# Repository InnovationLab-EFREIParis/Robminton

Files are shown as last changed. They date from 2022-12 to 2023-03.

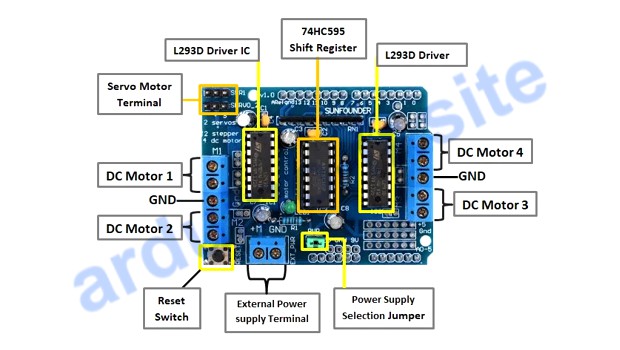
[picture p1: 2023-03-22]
03_ElecCode/1. Ramasseur/1. L293D Motor Drive Arduino Shield/1. Schematic/Components Schematic.jpg

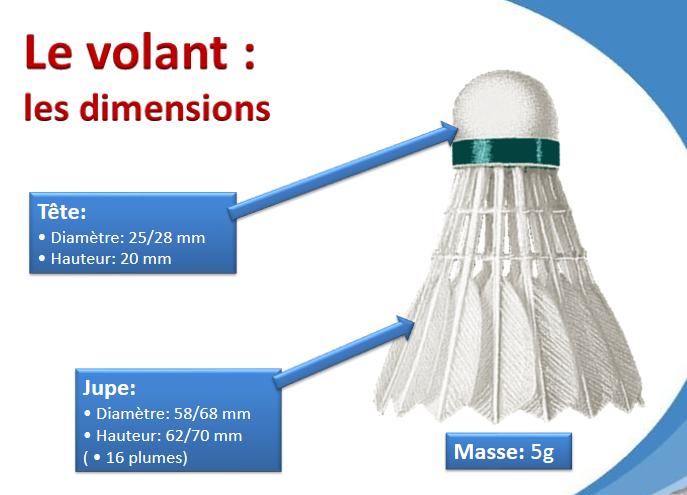
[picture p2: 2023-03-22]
03_ElecCode/0. Cave/dimension de volant.PNG

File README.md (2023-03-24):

# Robminton

Le projet a pour but de répondre à l'appel d'offre fait par la FFB (Fédération Française de Badminton). Il est composé de 2 parties, un robot ramasseur de volants ainsi qu'un robot lanceur de volants. Même si ce genre de produits existe déjà sur le marché (surtout côté lanceur) le but est quand même de produire un robot plus performant, open source et à moindre coût. 

Concernant les logiciels à avoir, il est nécessaire d'avoir SolidWorks afin d'utiliser au mieux les fichiers SW des pièces que nous avons modélisés. Il est aussi recommandé d'avoir un IDE (type CodeBlocks) pour tout ce qui est programme en C (calculatrice de paramètres du lanceur). Posséder une machine virtuel avec ROS et un IDE pour la programmation sur ST32 (type CubeIDE). 

Toutes les ressources que nous avons utilisées/produites sont présentes dans le git :

00_doc : contient toute la documentation que nous avons utilisé ou produit pendant le projet

01_mdl : contient les modélisation 3D que nous avons faites au cours du projet. Dedans ce sera le dossier SW qui sera le plus utile. Toutes les pièces/assemblages y sont. 

02_src : contient tout les codes sources utilisés pour faire fonctionner les moteurs présents dans nos robots. 

03_elec : contient de la documentation détaillée de toute l'électronique que nous utilisons que ce soit les cartes embarquées ou bien les moteurs. 

Nous avons fait en sorte que le projet parte sur de bonnes bases afin que les prochains groupes puissent travailler sur la partie plus intéressante du projet c'est à dire faire des tests. La modélisation du châssis du robot ramasseur est faite, il ne manque que quelques découpes à faire et des équerres à commander. Les moteurs fonctionnent avec le code que nous avons mis sur le Git il suffira de gérer les 4 moteurs en même temps. Le chemin pour y arriver est le suivant : Robminton/03_elec/1. Ramasseur/3. STM32 Nucleo-64/0. Code/1. L293D Motor1 Drive Arduino Shield/L293_Shield/

Il faudra cependant trouver une solution pour que le robot puisse ramasser tout les volants (plusieurs centaines de volants) rapidment donc sûrement revoir le système de stockage. Niveau lanceur toute la partie théorique à été faite et donc ne sera plus à refaire. Un dispositif pour le lanceur a été mis en place il ne reste qu'à l'implémenter sur une structure (en profilé), un croquis est disponible dans 00_src pour mieux comprendre. 

Le matériel que nous avons utilisé sera présent dans le casier Robminton à l'I-lab, ou bien sera à récupérer auprès des encadrants du projet (Rémi GRIOT/Elizabeth Colin). Un inventaire sera aussi disponible dans le dossier 00_doc afin que les prochains groupes puissent savoir ce qu'il manque, ce qu'il commander ...

Equipe : AMADO Daniel, BERBEROVIC Amon, LIENG Antoine, PUSZYNSKI Hugo, VACHEROT Tristan

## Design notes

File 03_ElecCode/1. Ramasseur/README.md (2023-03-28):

# Ramasseur Folder
Ce dossier contient tous les codes et documentations du ramasseur.

## Contenu des fichiers
* `1. L293D Motor Drive Arduino Shield`: ce dossier est consacré à la carte conçu pour être utilisée avec la carte STM32 pour contrôler les moteurs du robot.
* `2. CQRobot DC Geared Motor with Encoder`: ce dossier est consacré aux moteurs électriques à courant continu à engrenages avec un encodeur intégré.
* `3. STM32 Nucleo-64`: ce dossier est consacré aux codes et aux schémas électroniques entre la carte STM32 et les autres composants du robot.
* `4. Raspberry Pi3`: ce dossier est consacré aux programmes et aux librairies utilisés pour manipuler la carte STM32 avec une Raspberry.

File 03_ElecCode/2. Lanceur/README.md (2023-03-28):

# Lanceur Folder
Ce dossier contient tous les codes et documentations du lanceur.

## Contenu des fichiers
* `1. Racerstar BR2306S 2400KV`: ce dossier est consacré au moteur sans balais pour les drones de course FPV qui sont ici utilisés pour le lanceur.
* `2. ESC`: ce dossier est consacré aux dispositifs électroniques qui contrôlent la vitesse et la direction des moteur sans balais tels que ceux utilisés dans le lanceur.
* `3. STM32 Nucleo-64`: ce dossier est consacré aux codes et aux schémas électroniques entre la carte STM32 et les autres composants du lanceur.
* `4. Raspberry Pi3`: ce dossier est consacré aux programmes et aux librairies utilisés pour manipuler la carte STM32 avec une la Raspberry.

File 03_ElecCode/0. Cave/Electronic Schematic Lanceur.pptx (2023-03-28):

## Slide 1

15 V

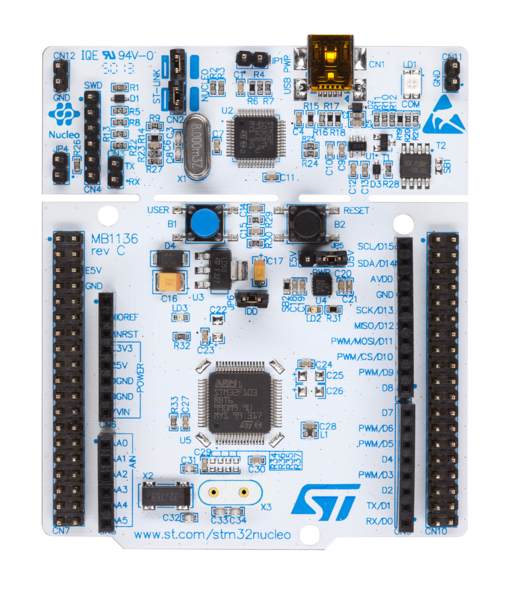
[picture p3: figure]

M

ESC

ESC

M

PWM_PIN1

PWM_PIN2

Raspberry PI 3

Serial.read()

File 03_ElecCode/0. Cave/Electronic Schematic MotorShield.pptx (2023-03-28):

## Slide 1


M2

M2

M1

M1

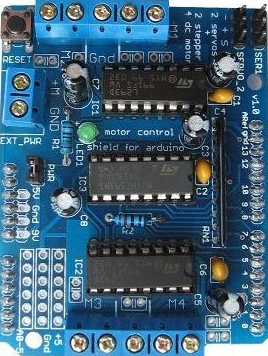
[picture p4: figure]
Shield controle de moteurs L293D Arduino

GND

V++

M4

M4

M4

M4

GND

- 12v +

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
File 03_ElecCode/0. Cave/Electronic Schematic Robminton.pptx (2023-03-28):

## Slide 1

Raspberry PI 3

Serial.read()

GND

- 12v +

V++

M1

M1

M1ENCB

M1ENCA

5V

GND

M1

M2

M2

M2ENCB

M2ENCA

5V

GND

M2


M2

M2

M1

M1

GND

V++

Shield controle de moteurs L293D Arduino

M4ENCA

M4ENCB

GND

5V

M3ENCA

M1ENCA

M1ENCB

M2ENCA

M2ENCB

M3ENCB

M4

M4

M4

M4

M3

M3

M3ENCB

M3ENCA

5V

GND

M3

M4

M4

M4ENCB

M4ENCA

5V

GND

M4

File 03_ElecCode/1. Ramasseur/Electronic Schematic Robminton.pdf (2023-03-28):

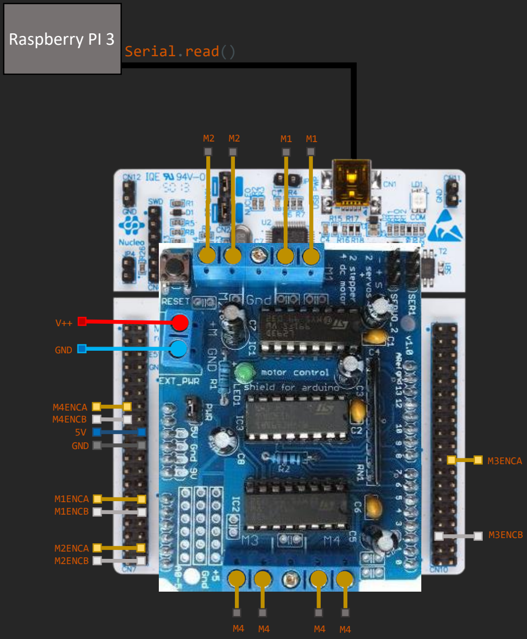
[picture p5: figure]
Serial.read(); Raspberry PI 3; GND; 5V GND; M1ENCA M1ENCB; M2ENCA M2ENCB; M3ENCA; M3ENCB; M4ENCA M4ENCB

M1 | M1ENCA M1ENCB

5V

GND

M1

M1

M2 | M2ENCA M2ENCB

5V

GND

M2

M2

M3 | M3ENCA M3ENCB

5V

GND

M3

M3

M4 | M4ENCA M4ENCB

5V

GND

M4

M4

GND | - 12v + | V++

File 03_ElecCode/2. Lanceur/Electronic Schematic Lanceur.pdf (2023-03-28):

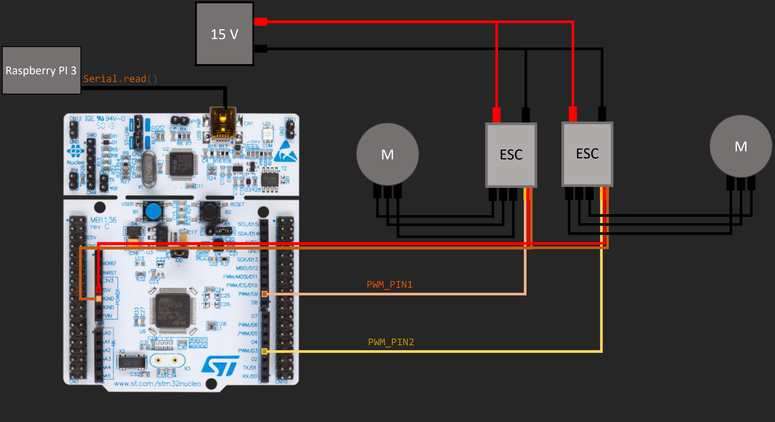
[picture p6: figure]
ESC; PWM_PIN1; PWM_PIN2; Serial.read(); Raspberry PI 3

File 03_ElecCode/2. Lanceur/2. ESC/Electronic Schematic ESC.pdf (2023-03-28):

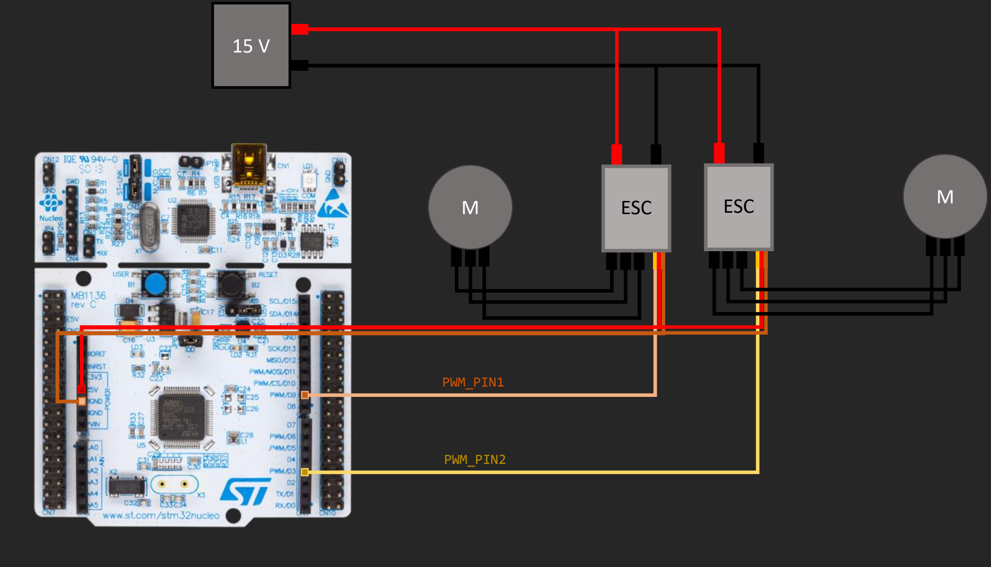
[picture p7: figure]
ESC; PWM_PIN1; PWM_PIN2

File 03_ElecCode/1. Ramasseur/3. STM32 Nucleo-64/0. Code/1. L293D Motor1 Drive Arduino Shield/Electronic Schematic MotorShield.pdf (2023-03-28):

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
GND | - 12v + | V++

V++

GND

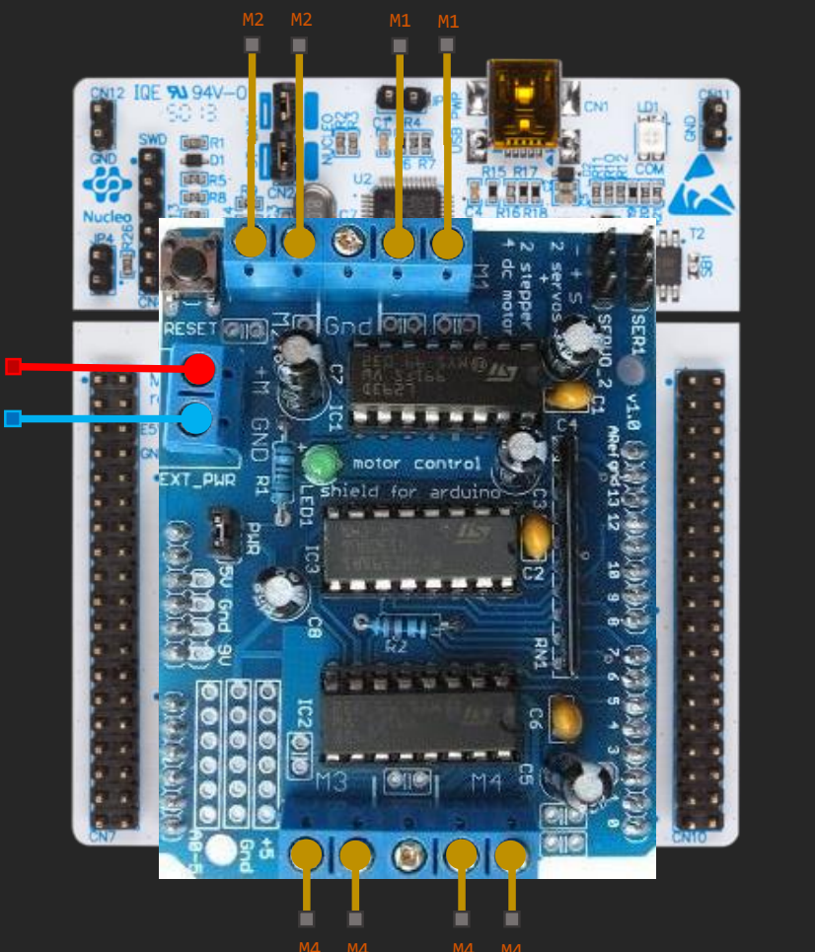
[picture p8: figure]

M4 | M4 | M4 | M4

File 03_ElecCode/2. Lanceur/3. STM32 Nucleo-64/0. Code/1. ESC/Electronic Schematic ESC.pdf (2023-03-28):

ESC; PWM_PIN1; PWM_PIN2

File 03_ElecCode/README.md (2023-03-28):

# ElecCode Folder
Ce dossier a été créé pour réunir tous les codes et documentations pour l'utilisation du matériel électronique de ce projet.

## Contenu des fichiers
* `0.Cave`: ce dossier contient tout les fichiers `.word` et `.pw` qui ont servi à la réalisation des documentations et schémas.
* `1.Ramasseur`: ce dossier contient les codes et les documentations pour le ramasseur.
* `2.Lanceur`: ce dossier contient les codes et documentations pour le lanceur.

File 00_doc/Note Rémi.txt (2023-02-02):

* Robminton
** Ramasseur
Detection d'obstacle (fauteuil-pied de chaise-personne)
Empiler les volants les uns dans les autres
600-700 volants max
200 - 300 volants nominale
Lancer 16 volants en 10 secondes
** Lanceur
lancé reproductible, toujours le même lancé
multi lanceur OK
badenko constructeur: attention usure des volants
https://www.youtube.com/watch?v=XtE6wyeD8XM
signalétique (compte à rebours)
réglage vitesse/angle
vitesse max en smatsh record 400km/h sortie raquette - nominal 200 km/h
cadence 20 volants - 10 secondes 
Hugo : aspect mécanique
Amon : ROS

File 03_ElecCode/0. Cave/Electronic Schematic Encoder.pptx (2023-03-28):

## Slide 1

M1

M4

M3


M2

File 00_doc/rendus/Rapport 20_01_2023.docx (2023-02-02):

Rapport de la réunion du 06/01/2023

Fin du premier run pour notre équipe, les objectifs ont tous été atteints dans la plupart. En effet, au cours de la réunion de nouvelles contraintes ont été données qui affecteront l’avancement de notre projet. C’est aussi le jour ou nous avons présenté notre projet au fab lab.

Remarques :

Robot ramasseur :

-Les jupes de protection ne vont sûrement pas tenir

-Songer à orienter les roues vers l’intérieur du robot et si possible abaisser le châssis pour éviter que les volants passent en dessous

-On a besoin de 7 mètres voire un peu plus et une vingtaine d’équerres juste pour le châssis.

Entonnoir :

-Revoir la fixation de l’entonnoir sur le châssis car les équerres modélisées ne vont pas tenir.

-Favoriser les équerres angle droit dans les deux robots, c’est plus simple et plus solide.

-On adopte une forme de râteau pour l’entonnoir. Comme ca on garde les angle droits partout

STM32/RasPi :

-Communication faite entre les deux cartes, on peut gérer les LEDS maintenant il faut gérer les moteurs et les roues.

Lanceur :

-Bonne nouvelle qu’on ait avancé sur les équations

-Choix et définition d’une trajectoire théorique (18° vers le haut et on envoie a 200km/h environs) on va essayer de s’en tenir pour nos tests.

-Voir comment intégrer la cadence dans le lanceur (20 volants/10-15 secondes).

-Continuer la théorie sur la gestion de trajectoire

Prochain Run du 10/02/2023 :

Ramasseur :

-Faire valider les dernières modifs sur le design et faire le montage (inclus l’entonnoir)

-Penser à l’agencement de la batterie, des cartes etc

Hardware/software :

-faire fonctionner les moteurs/roues, imprimer les protections de cartes et de quoi les fixer aux châssis.

Lanceur :

-Continuer a travailler sur les équations : pour une distance voulue combien on doit avoir en vitesse et en angle.

-Chercher un lien entre la vitesse de rotation des volants et la vitesse du volant

A noter que chacun peut aller sur un autre pôle si besoin (principalement Hardware/soft puisque Amon est tout seul)

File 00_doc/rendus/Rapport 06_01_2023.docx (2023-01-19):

Rapport de la réunion du 06/01/2023

Au cours de cette séance nous avons présenté notre avancement aux encadrants de notre projets afin de récupérer le maximum de remarques et de critiques. Le but étant de corriger notre tir et de partir dans la bonne direction.

Remarques :

Robot ramasseur :

-Revoir la forme des protection de roues

-Ne pas seulement songer à protéger les roues des volants

-Veiller à ce que les volants n’aillent pas en dessous du robot

Entonnoir :

-Songer à une version avec du profilé d’alu

-Faire en sorte que l’entonnoir soit fixé au robot avec du profilé et pas juste à l’arrache comme avant.

-Rouleaux fixés sur le profilé mais on garde les planches sur le côté

STM32/RasPi :

-Utiliser Ros Serial pour la communication entre les deux cartes

Lanceur :

-Revoir les moteurs utilisés pour le lanceur

-Modéliser une structure (comme un châssis)

-Revoir l’étude sur le badminton

-Songer à passer par les équations pour obtenir la trajectoire souhaitée

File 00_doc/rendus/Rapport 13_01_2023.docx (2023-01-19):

Rapport réunion du 13/01/2023

Dernière séance de projet avant la fin du « RUN » et de la présentation à l’Innovation-Lab. Poursuite de la présentation des avancements, cette fois-ci en prenant en compte les remarques de la semaine passée.

Robot ramasseur :

-Présentation du nouveau dispositif pour empêcher les volants de passer sous le robot

-Couvre toute les côtés latéraux du ramasseur et est facilement montable/démontable

-Limite à 5mm du sol, hauteur à revoir pour éviter que les volants ne s’y coincent

-Présentation de l’entonnoir à base de profilé d’aluminium

-Présentation des équerres modélisées sur SW

-Les rouleaux montés sur le profilé ce qui nous permettra de les déplacer facilement.

-Fixation sur le ramasseur

-Penser à veiller a ce que l’entonnoir ne contrebalance pas et ne perturbe l’équilibre du robot.

-Présentation de la communication STM32-Raspi rendue possible

-Communication faite entre les deux cartes (possibilité d’allumer une LED)

-Design de boitier trouvé pour les cartes.

-Trouver les bons moteurs/contrôleurs pour le robot et adapté aux cartes

-Etude sur le lanceur et prototypage

-Présentation du prototypage modélisé sur SW (voir slides)

-Présentation des paramètres importants pour gérer la trajectoire du robot.

-Entretien prévu mardi pour faire l’étude de la trajectoire

Choses à faire pour la présentation :

-Schéma fonctionnel pour les deux robots

-Présenter l’évolution entre le robot de l’an dernier et celui qu’on veut faire aujourd’hui

-Présenter l’évolution des designs

-Présenter une étude solide/pertinente sur la trajectoire du volant.

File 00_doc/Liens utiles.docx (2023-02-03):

Documentation utile Lanceur :

Lien de la chaine d’un gars qui construit un kit Lanceur de volant :

https://www.youtube.com/@baddy7061/videos

https://www.youtube.com/watch?v=CvGgPDdLS_0

Un gars qui fait des tests pour la trajectoire en fonction des RPM d’autres paramètres sont intéressants aussi

https://www.warse.org/IJATCSE/static/pdf/file/ijatcse242952020.pdf

Badenco :

https://fr.made-in-china.com/co_siboasi/product_Promotional-Siboasi-Badminton-Shuttlecock-Launcher-Machine-S4025-_rgoeyensg.html

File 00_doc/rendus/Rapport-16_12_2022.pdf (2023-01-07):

# Rapport de la réunion du 16/12/2022

Le but de cette séance était de récupérer le plus d’informations et de matériel afin de pouvoir travailler pendant les vacances sans pour autant avoir à revenir à l’école. Hugo et Antoine sont allés prendre les mesures du robot ramasseur de volants au Research Lab afin de pouvoir commencer la modélisation sur Solid Works. Tristan, Daniel et Amon sont restés avec Madame Colin afin de pouvoir définir les tâches à faire pour la bonne réalisation du robot.

# Les tâches sont les suivantes :

## Robot Ramasseur :

Navigation :

- Déplacement sur le terrain
- Détection de lignes (limites du terrain)
- Détection d’obstacles

Traitement du volant :

- Collecter les volants
- Stocker et les empiler
- Déposer les volants au bord du terrain

Fabrication :

- Châssis
- Espace de stockage
- Entonnoir

Assemblage puis tests

Code :

- Programmation des moteurs
- Programmation de la trajectoire
- Détection des lignes
- Détection des obstacles
- Détection du stockage de volants

## Robot lanceur :

Etude :

- Lancer régulier
- Vitesse de propulsion
- Cadence
- Inclinaison
- Hauteur

Fabrication :

- Rouleau
- Rampe
- Support

Code :

- Programmation des moteurs
- Programmation du lancer de volants

# Prochains objectifs :

-Avancer chacun de son côté (selon les pôles définis)

-Préparer une présentation des avancements pour le vendredi de la rentrée.

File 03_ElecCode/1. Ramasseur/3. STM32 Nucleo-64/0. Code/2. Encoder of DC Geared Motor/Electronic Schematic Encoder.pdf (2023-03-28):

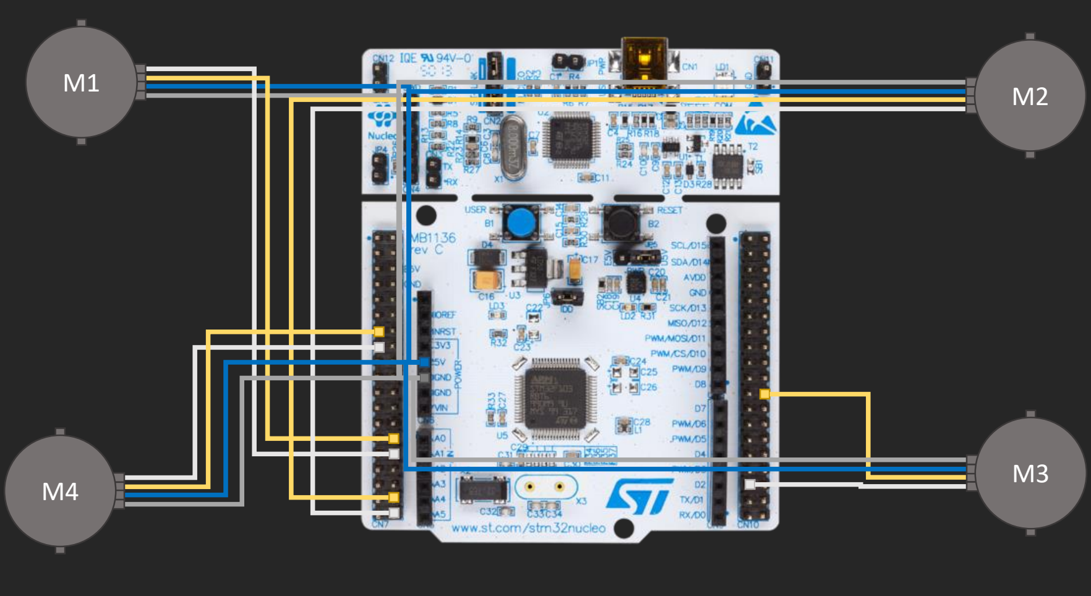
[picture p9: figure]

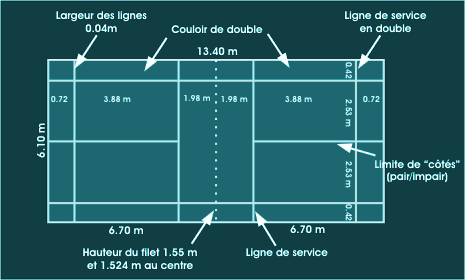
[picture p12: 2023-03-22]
03_ElecCode/0. Cave/dimension de terrain.png

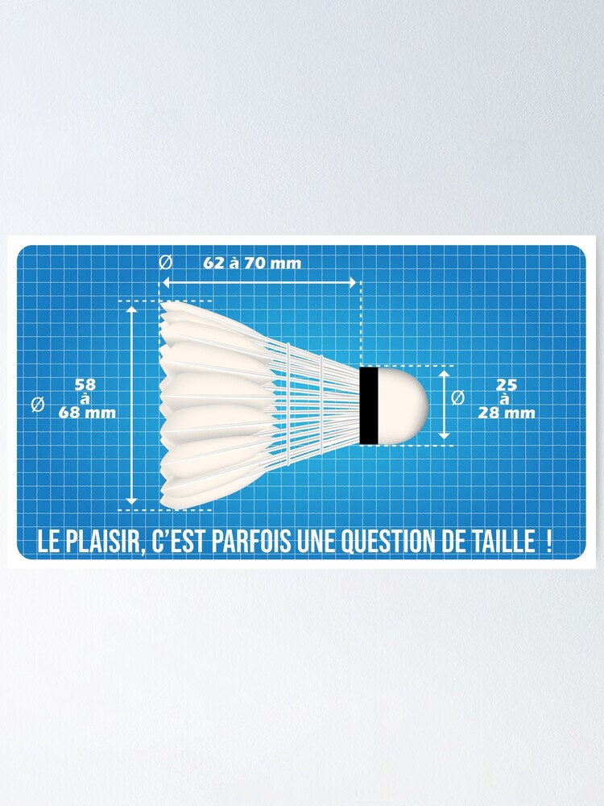
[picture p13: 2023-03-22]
03_ElecCode/0. Cave/dimension de volant de Badminton.jpg

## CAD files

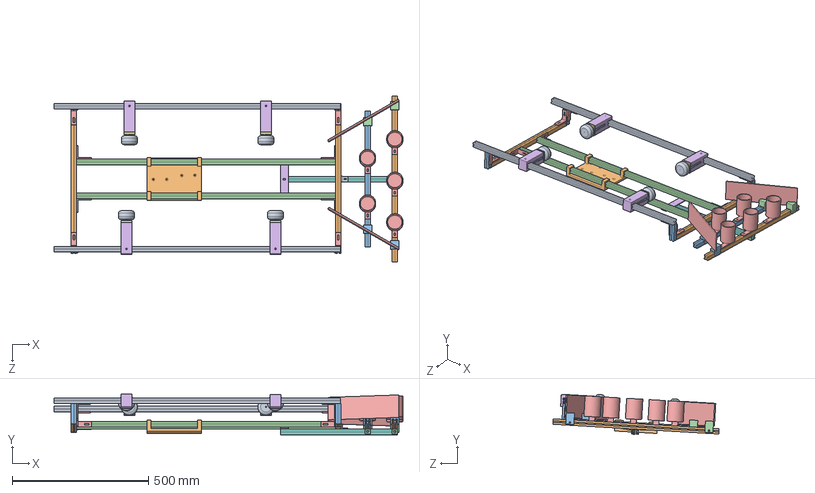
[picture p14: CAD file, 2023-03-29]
01_mdl/SW/Assemblage final/robot_entonnoir_V4.SLDASM
1280.1 x 148.6 x 610.1 mm
profil_alu_rs20_efrei - longueur x 2
profil_alu_rs20_efrei x 2
profil_alu_rs20_efrei - 5,5cm x 4
profil_alu_rs20_efrei - 95cm x 2
equerre x 12
fixation_plate_entonnoir_arriere_V3
fixation_plate_entonnoir_avant_V1
profil_alu_rs20_efrei_entonnoir
equerre_2_V1
profil_alu_rs20_efrei_rouleau_2
profil_alu_rs20_efrei_rouleau_3
equerre_V2 x 2
rouleau_V3 x 5
support moteur x 4
couvercle support moteur x 4
Modélisation_moteur x 4
Modélisation_roue x 4
Support Hardware
accroche_cote_droite x 2
accroche_cote_gauche x 2
plaque x 2

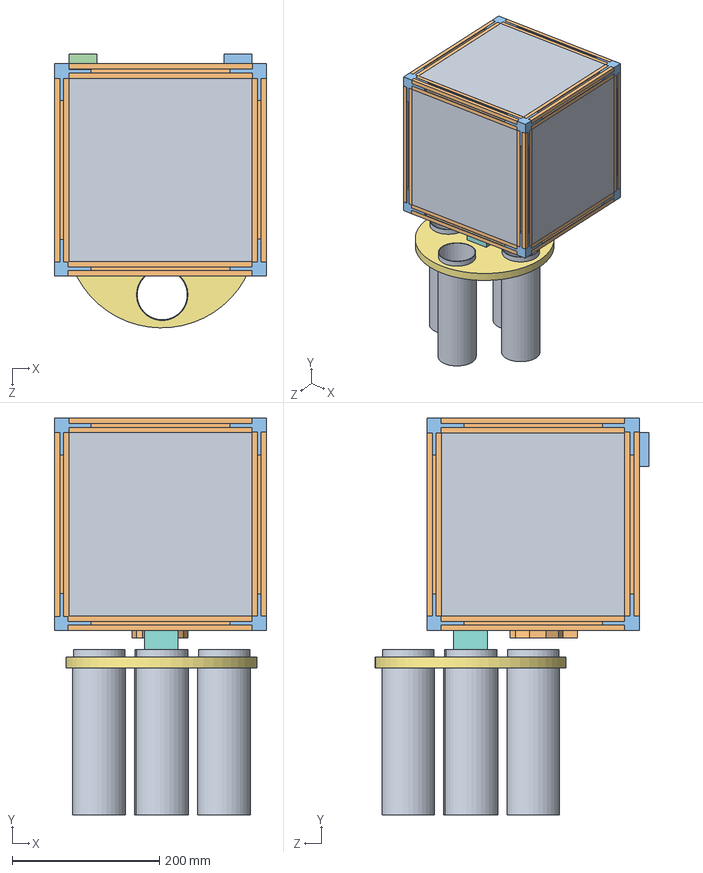
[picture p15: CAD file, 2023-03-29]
01_mdl/SW/Lanceur/cube_lanceur_final.SLDASM
289.0 x 540.0 x 372.3 mm
lanceur_25_25_vrai x 4
profil_alu_cube_25cm x 12
accroche x 8
lanceur_toit_25_25
rampe_lanceur
modèle3D_Nema17 x 2
Support_cylindre_volant
support_moteur_nema17_toit
Support_volant_x4 x 4
Modèle3D_pince
support_moteur_nema17_cylindre
support_soutenir_poids_base

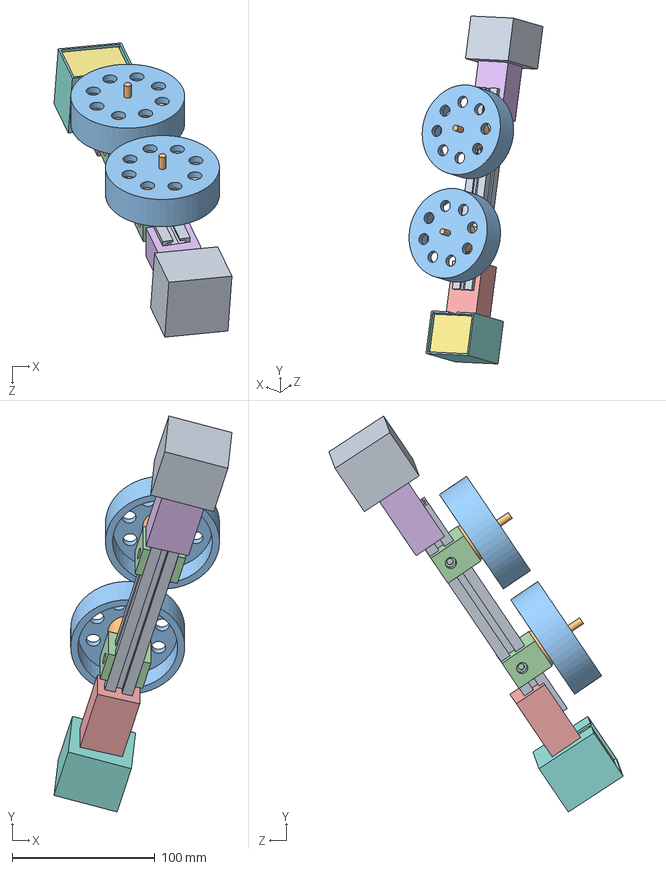
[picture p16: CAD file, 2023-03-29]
01_mdl/SW/Lanceur/système_lancement.SLDASM
124.8 x 277.7 x 206.4 mm
profil_alu_cube_18cm
modèle3D_moteur_drone x 2
9e_cylindre_sans_trous-système_8cm x 2
support_moteur_drone_VF_mesure_vis x 2
accroche_moteur_profilé_VF
accroche_moteur_profilé_VF_soutenir
modèle3D_Nema17
support_moteur_nema17_cylindre_sans_accroche
support_soutenir_poids_base_sans_accroche_VF

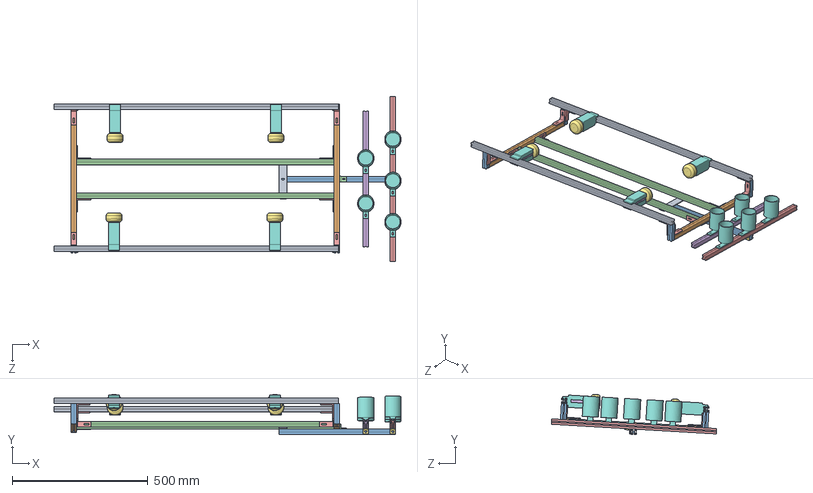
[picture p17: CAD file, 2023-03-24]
01_mdl/SW/entonnoir/robot_entonnoir_V4.SLDASM
1280.1 x 148.9 x 610.1 mm
profil_alu_rs20_efrei - longueur x 2
profil_alu_rs20_efrei x 2
profil_alu_rs20_efrei - 5,5cm x 4
profil_alu_rs20_efrei - 95cm x 2
equerre x 12
Modélisation_moteur x 4
Modélisation_roue x 4
support moteur V2 x 4
fixation_plate_entonnoir_arriere_V3
fixation_plate_entonnoir_avant_V1
profil_alu_rs20_efrei_entonnoir
equerre_2_V1
profil_alu_rs20_efrei_rouleau_2
profil_alu_rs20_efrei_rouleau_3
equerre_V2 x 2
rouleau_V3 x 5

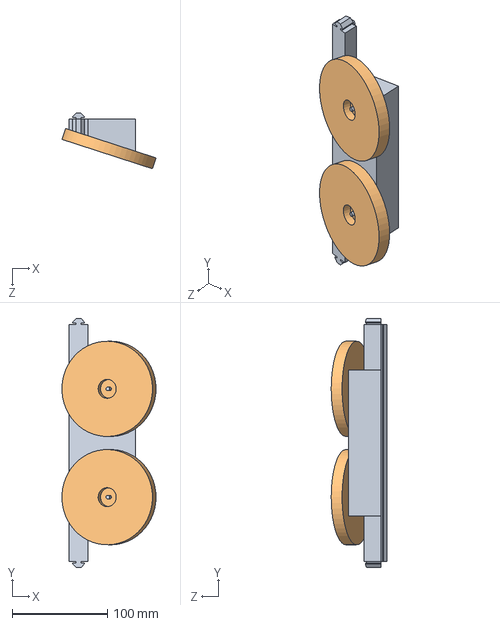
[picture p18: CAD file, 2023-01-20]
01_mdl/SW/Lanceur_pieces_tests/accrochage_demo.SLDASM
98.8 x 261.4 x 58.3 mm
base_moteur_angle_18
7e_cylindre_sans_trous_cube x 2

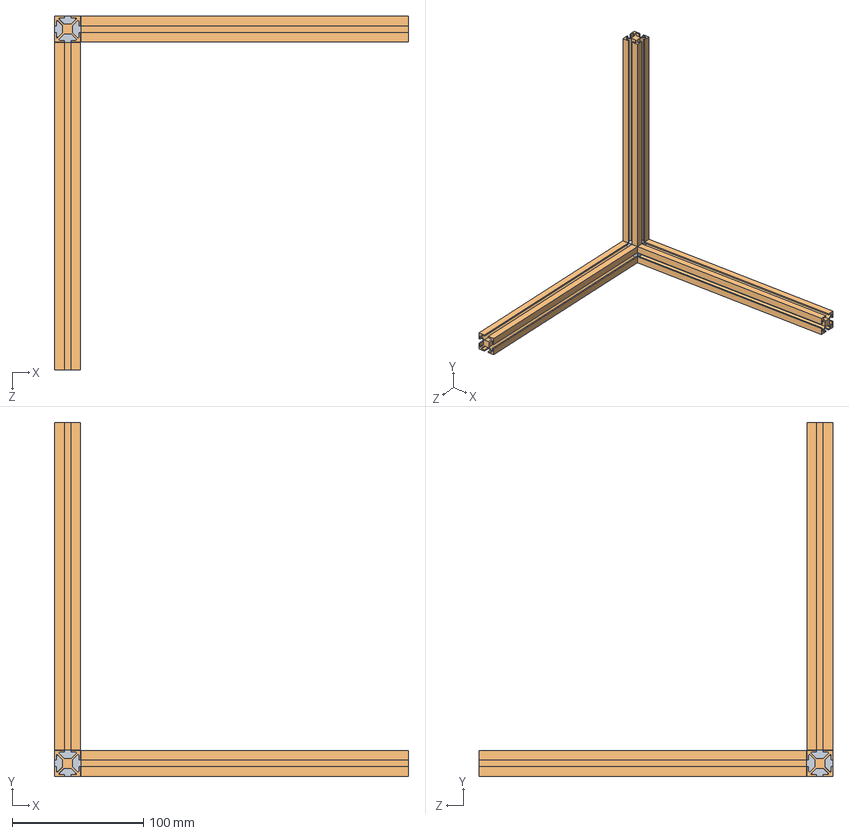
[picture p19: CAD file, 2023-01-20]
01_mdl/SW/Lanceur_pieces_tests/support_demo.SLDASM
270.0 x 270.0 x 270.0 mm
accroche
profil_alu_cube_25cm x 3

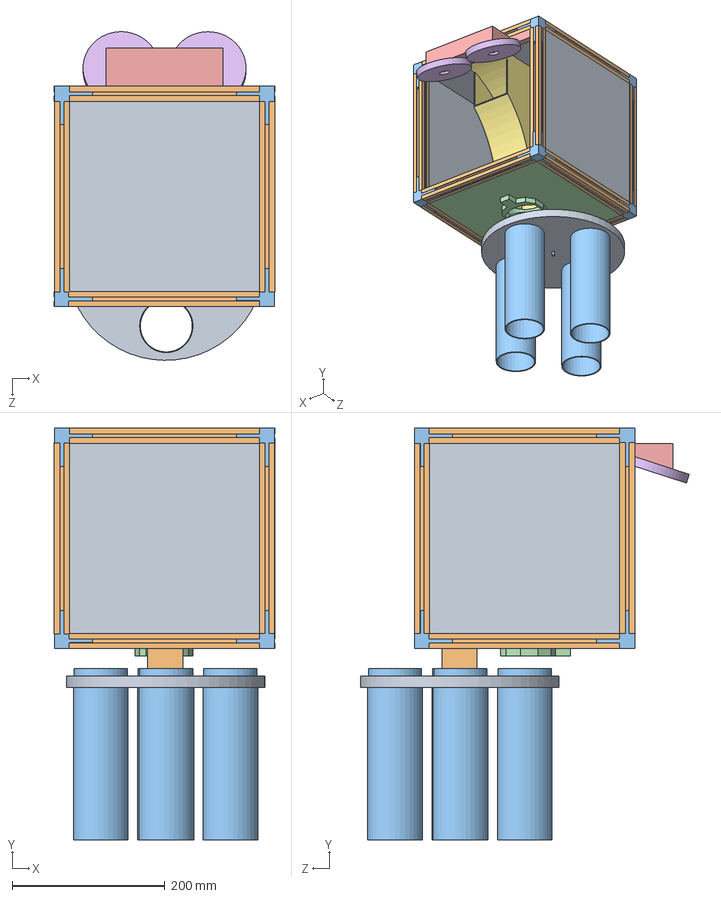
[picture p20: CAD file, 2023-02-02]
01_mdl/SW/Lanceur/cube_lanceur.SLDASM
289.0 x 540.0 x 430.7 mm
lanceur_25_25_vrai x 4
profil_alu_cube_25cm x 12
accroche x 8
lanceur_toit_25_25
base_moteur_angle_18
7e_cylindre_sans_trous_cube x 2
rampe_lanceur
modèle3D_Nema17
Support_cylindre_volant
support_moteur_nema17_toit
Support_volant_x4 x 4
Modèle3D_pince

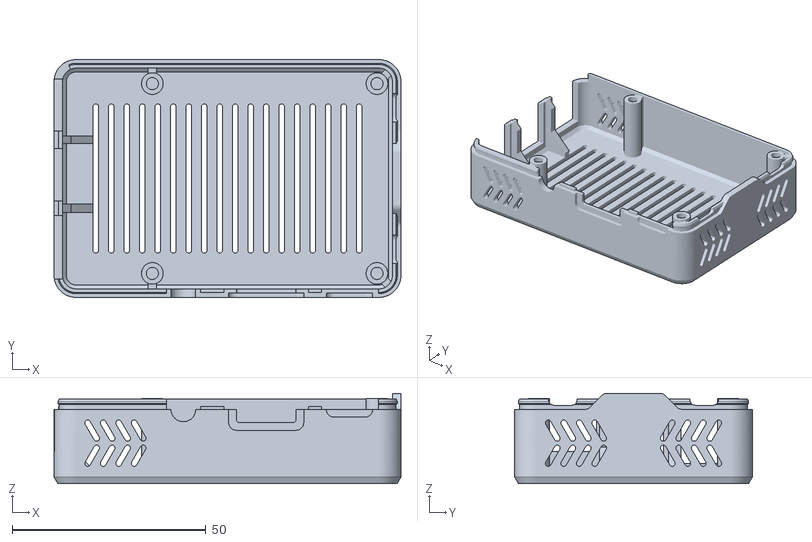
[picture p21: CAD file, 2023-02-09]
01_mdl/STL/Boite_rapsberry/Top_H20_Slots_SM.stl
89.6 x 61.4 x 23.4

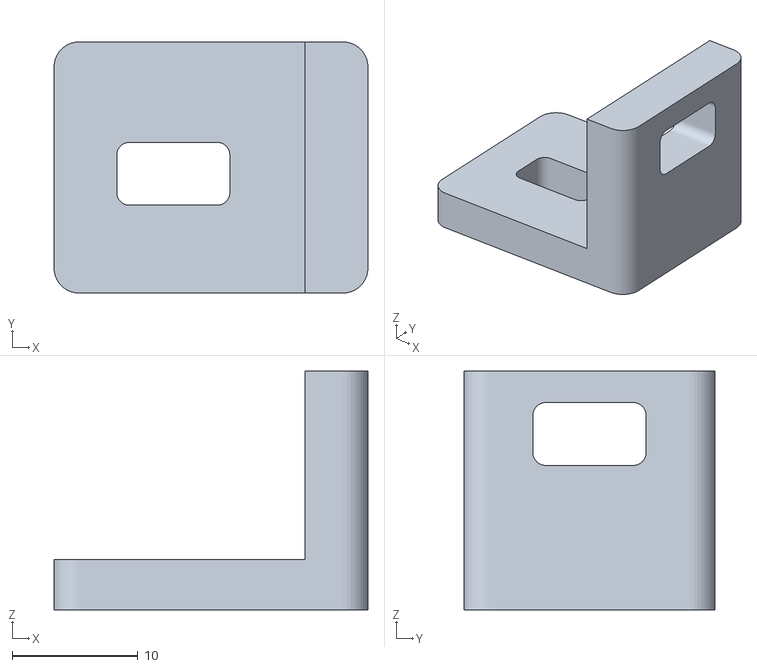
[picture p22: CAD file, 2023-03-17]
01_mdl/STL/equerre_2_V1.STL
25.0 x 20.0 x 19.0

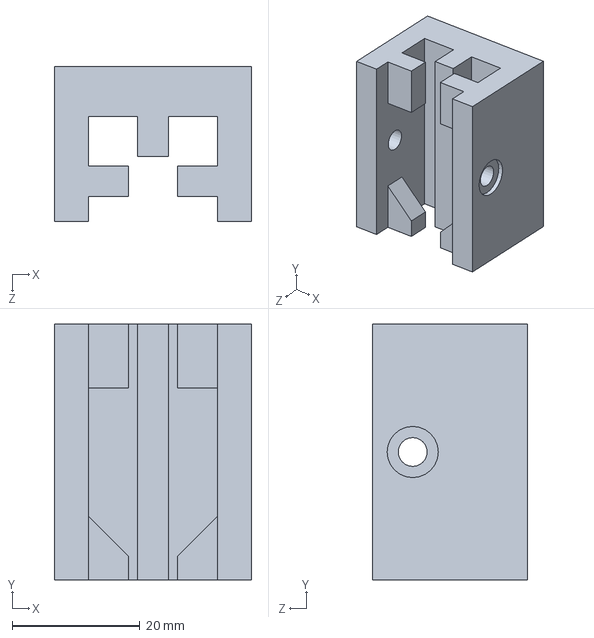
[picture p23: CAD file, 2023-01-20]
01_mdl/SW/Divers/support_moteur_rs4.SLDPRT
30.8 x 40.0 x 24.1 mm

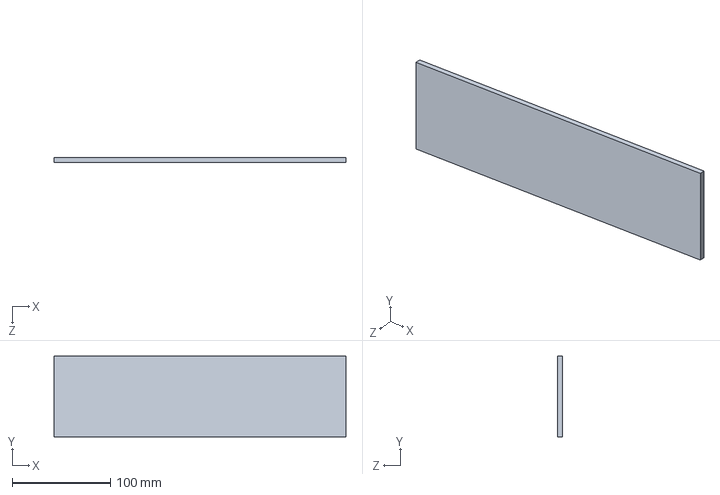
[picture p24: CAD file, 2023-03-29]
01_mdl/SW/entonnoir/plaque.SLDPRT
297.5 x 82.5 x 5.00 mm

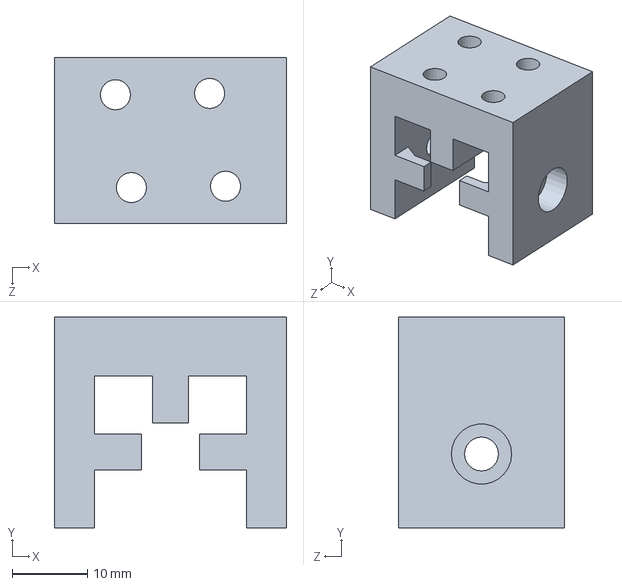
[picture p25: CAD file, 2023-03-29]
01_mdl/SW/Lanceur/support_moteur_drone_VF_mesure_vis.SLDPRT
30.8 x 28.0 x 22.0 mm

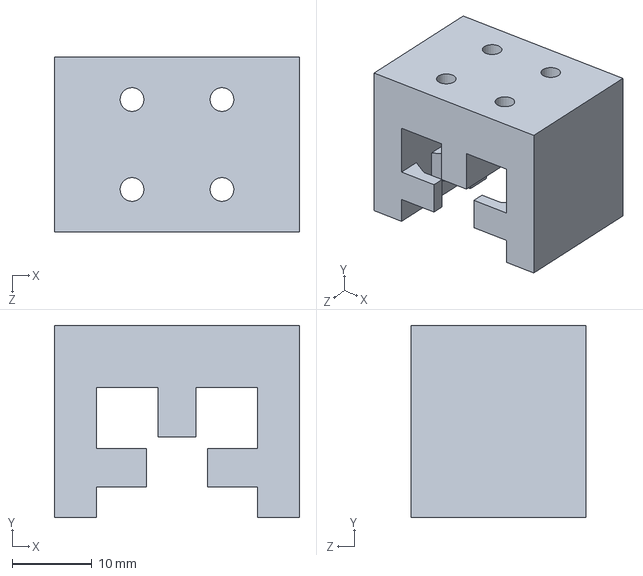
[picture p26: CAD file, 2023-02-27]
01_mdl/SW/Lanceur_pieces_tests/support_moteur_drone_VF.SLDPRT
30.8 x 24.1 x 22.0 mm

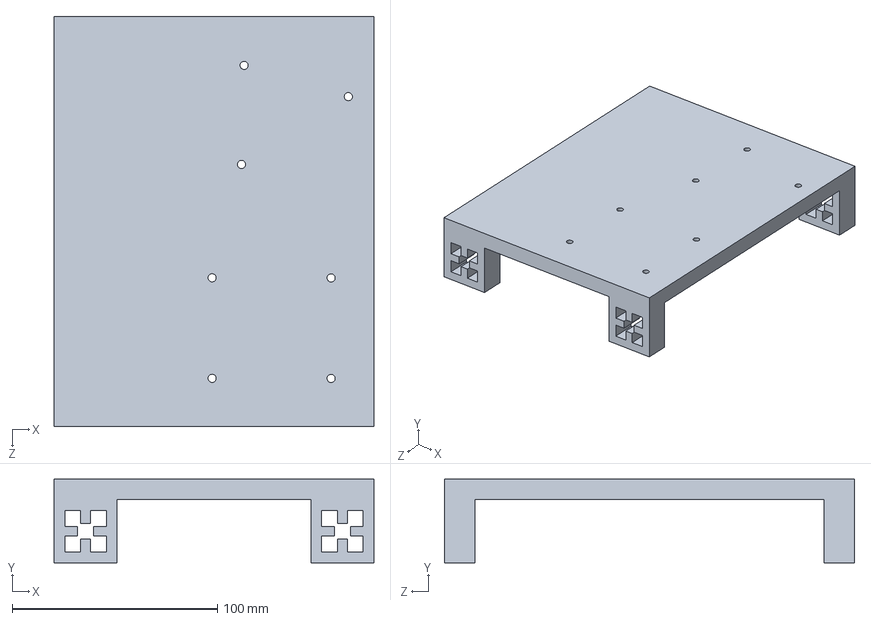
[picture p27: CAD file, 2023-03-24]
01_mdl/SW/Support hardware/Support Hardware.SLDPRT
156.0 x 40.8 x 200.0 mm

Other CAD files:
01_mdl/SW/Support moteur/support moteur.SLDPRT
01_mdl/SW/support_STM32/supportNucleo_rs20.SLDPRT
01_mdl/STL/Boite_rapsberry/Bottom_Hex_SM.stl
01_mdl/STL/equerre_V2.STL
01_mdl/STL/fixation_plate_entonnoir_arriere_V3.STL
01_mdl/STL/fixation_plate_entonnoir_avant_V1.STL
01_mdl/STL/rouleau_V3.STL
01_mdl/SW/Divers/Modélisation_moteur.SLDPRT
01_mdl/SW/Divers/Modélisation_roue.SLDPRT
01_mdl/SW/Divers/equerre.SLDPRT
01_mdl/SW/Divers/nut_rs20.SLDPRT
01_mdl/SW/Divers/profil_alu_rs20_efrei - 5,5cm.SLDPRT
01_mdl/SW/Divers/profil_alu_rs20_efrei - 95cm.SLDPRT
01_mdl/SW/Divers/profil_alu_rs20_efrei - longueur.SLDPRT
01_mdl/SW/Divers/profil_alu_rs20_efrei.SLDPRT
01_mdl/SW/Lanceur/9e_cylindre_sans_trous-système_8cm.SLDPRT
01_mdl/SW/Lanceur/9e_cylindre_sans_trous-système_8cm.STL
01_mdl/SW/Lanceur/Accroche_moteur_profilé.STL
01_mdl/SW/Lanceur/Modèle3D_pince.SLDPRT
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

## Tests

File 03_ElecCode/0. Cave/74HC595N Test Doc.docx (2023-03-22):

# INTRODUCTION

SN74HC595N est un circuit intégré (CI) de décalage de registre à décalage parallèle-série à huit bits fabriqués par Texas Instruments. Il appartient à la famille de circuits intégrés de la série 74HC et est couramment utilisé dans les applications électroniques pour étendre le nombre de broches d'un microcontrôleur, d'un microprocesseur ou d'un FPGA.

Le SN74HC595N a huit sorties parallèles qui peuvent être contrôlées individuellement et une sortie en série qui permet de déplacer les données hors du circuit. Il est utilisé pour contrôler des LED, des afficheurs à sept segments, des relais, des moteurs pas à pas, des écrans LCD et d'autres périphériques d'entrée/sortie dans les projets électroniques.

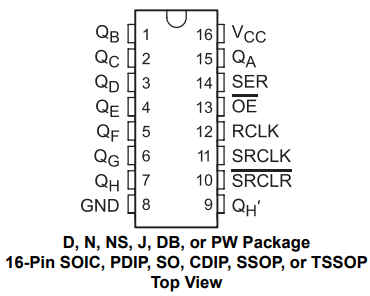
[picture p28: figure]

« Registre SN74HC595N »

# MONTAGE

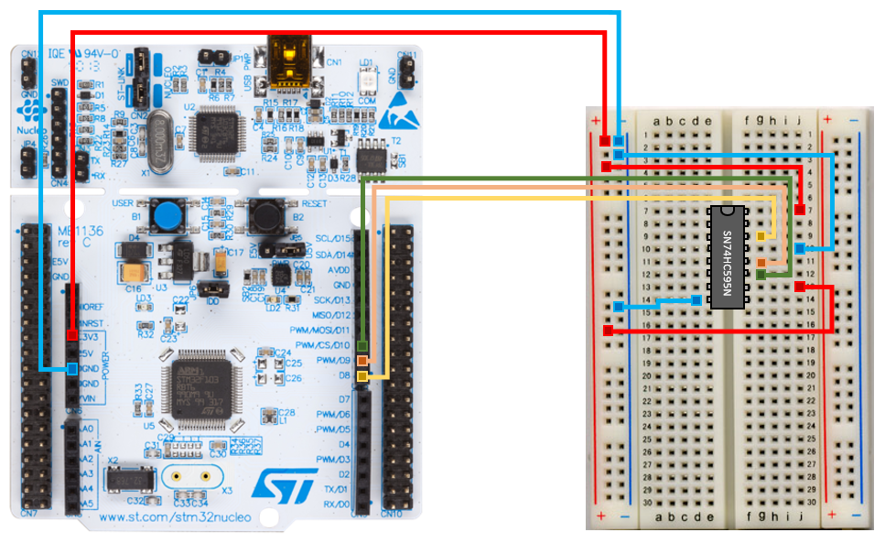
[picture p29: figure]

« Montage électrique »

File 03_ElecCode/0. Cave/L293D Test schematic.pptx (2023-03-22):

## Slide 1

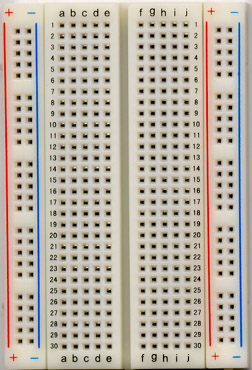
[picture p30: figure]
LOCODUINO - Les indispensables du prototypage

M

L293D

- 12v +

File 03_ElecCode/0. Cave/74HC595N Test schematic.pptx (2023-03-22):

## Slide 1

LOCODUINO - Les indispensables du prototypage

SN74HC595N

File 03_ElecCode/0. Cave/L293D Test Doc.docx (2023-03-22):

# INTRODUCTION

Le L293D est un circuit intégré (CI) qui permet de piloter des moteurs à courant continu (DC) ou des moteurs pas-à-pas, il est fabriqué par plusieurs fabricants, y compris Texas Instruments et STMicroelectronics. Il est largement utilisé dans les projets électroniques qui impliquent le contrôle de moteurs, tels que les robots, les voitures télécommandées, les imprimantes 3D et les drones.

Le L293D est un double pont en H, ce qui signifie qu'il peut contrôler deux moteurs indépendamment. Il dispose de quatre sorties de puissance (deux pour chaque moteur), qui peuvent fournir jusqu'à 600 mA de courant par sortie, ainsi que de quatre entrées de commande (deux pour chaque moteur), qui permettent de contrôler la direction de rotation et la vitesse du moteur.

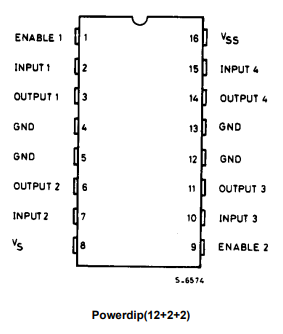
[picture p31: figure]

« Registre L293D »

# MONTAGE

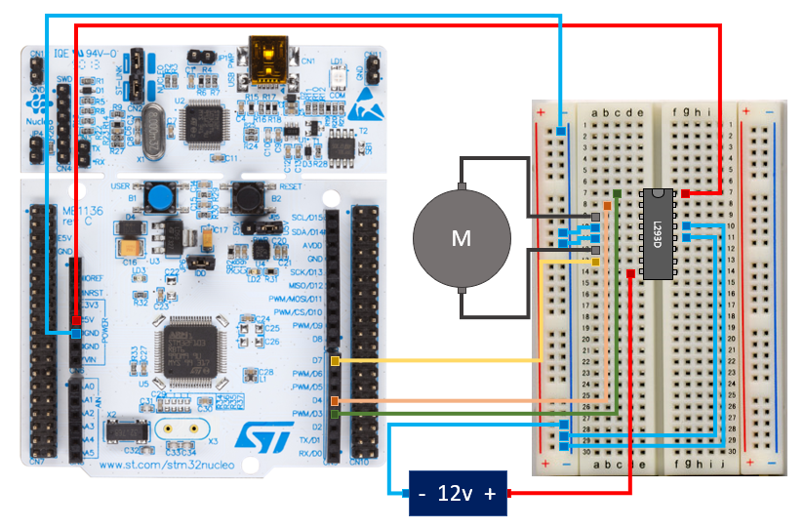
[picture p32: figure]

« Montage électrique »

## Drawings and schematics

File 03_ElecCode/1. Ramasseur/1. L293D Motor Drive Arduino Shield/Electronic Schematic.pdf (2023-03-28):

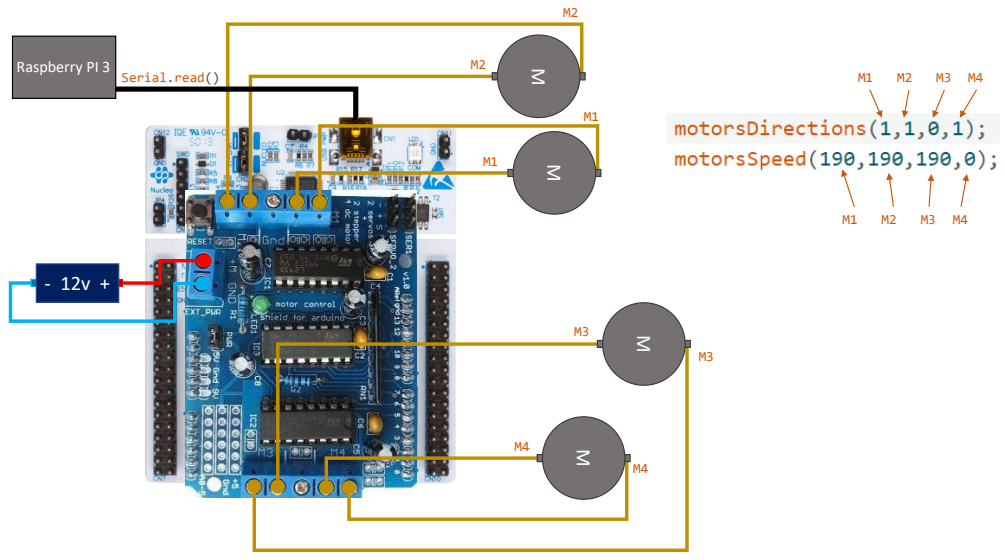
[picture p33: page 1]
Raspberry PI 3; Serial.read()

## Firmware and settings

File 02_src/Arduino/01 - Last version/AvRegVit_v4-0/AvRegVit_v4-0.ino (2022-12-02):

// Programme de balayage de la surface du terrain de badbigton par un robot équipé de roue mecanum

// ********************************************************************************************************************************************************************************
// Déclaration des constantes et des variables
// ********************************************************************************************************************************************************************************

// Déclaration des données du pont en H **************************************************************
#include <AFMotor.h>
AF_DCMotor motorAvDr(1);
AF_DCMotor motorAvGa(2);
AF_DCMotor motorArGa(3);
AF_DCMotor motorArDr(4);

// Déclaration des données des interruptions **********************************************************
int interruptPin_Dist = 2  ;
int interruptPin_MotAvGa = 18  ;
int interruptPin_MotAvDr = 19  ;
int interruptPin_MotArGa = 20  ;
int interruptPin_MotArDr = 21  ;
int compt_Dist = 1 ;
int compt_MotAvGa = 0;
int compt_MotAvDr = 0;
int compt_MotArGa = 0;
int compt_MotArDr = 0;
const int frequence_echantillonnage = 5;  // Fréquence d'exécution de l'asservissement (Xxx fois par seconde)

// Déclaration des caractéristique du moteur ***********************************************************
const int rapport_reducteur_MoteursDeplacement = 15;   // Rapport entre le nombre de tours de l'arbre moteur et de la roue
const int tick_par_tour_codeuse_MoteursDeplacement = 26;  //26 tick sur deux capteurs hall par capteur pour front montant et descendant, 13 sur un capteur 
const float DiametreRoue = 6.34 ;  // diametre de la roue 6,34 cm
float k_reductionMoteurs =(float)tick_par_tour_codeuse_MoteursDeplacement*(float)rapport_reducteur_MoteursDeplacement ;
float k_reductionDistance = 3.141592654*DiametreRoue/(float)tick_par_tour_codeuse_MoteursDeplacement/(float)rapport_reducteur_MoteursDeplacement ;

// Déclaration des caractéristique du robot ***********************************************************
int largeur_robot = 40 ; // cm
int longueur_demi_tour = 30 ; // cm

// Déclaration timer ***********************************************************************************
#include <SimpleTimer.h>
SimpleTimer timer_MoteursDeplacement;


// Déclaration des constantes et variables du PID *******************************************************
// Déclaration des constantes ********************************
float kp_MotAvGa = 8;     // coefficient proportionnel
float ki_MotAvGa = 5;       // Coefficient intégrateur
float kd_MotAvGa = 2.5;     // Coefficient dérivateur

float kp_MotAvDr = 8;     // coefficient proportionnel
float ki_MotAvDr= 5;       // Coefficient intégrateur
float kd_MotAvDr = 2.5;     // Coefficient dérivateur

float kp_MotArGa = 8;     // coefficient proportionnel
float ki_MotArGa = 5;       // Coefficient intégrateur
float kd_MotArGa = 2.5;     // Coefficient dérivateur

float kp_MotArDr = 8;     // coefficient proportionnel
float ki_MotArDr= 5;       // Coefficient intégrateur
float kd_MotArDr = 2.5;     // Coefficient dérivateur

// Initialisation des variables *******************************
float consigne_Dist = 100; //en cm
float Dist = 0;//en cm
bool Arret_Moteurs = false;
float consigne_des_moteurs = 5;

int vit_MotAvGa = 0;
float consigne_MotAvGa = 5; // consigne en nombre de tours de roue par seconde
float erreur_precedente_MotAvGa = consigne_MotAvGa;
float somme_erreur_MotAvGa = 0;

int vit_MotAvDr = 0;
float consigne_MotAvDr = consigne_MotAvGa; // consigne en nombre de tours de roue par seconde
float erreur_precedente_MotAvDr = consigne_MotAvDr;
float somme_erreur_MotAvDr = 0;

int vit_MotArGa = 0;
float consigne_MotArGa = consigne_MotAvGa; // consigne en nombre de tours de roue par seconde
float erreur_precedente_MotArGa = consigne_MotArGa;
float somme_erreur_MotArGa = 0;

int vit_MotArDr = 0;
float consigne_MotArDr = consigne_MotAvGa; // consigne en nombre de tours de roue par seconde
float erreur_precedente_MotArDr = consigne_MotArDr;
float somme_erreur_MotArDr = 0;


// Initialisation des données du séquenciel de balayage de la surface.
int Phase = 0;
int ref_Temps = 0 ;
int mes_Temps = 0 ;
int duration = 0 ;
int coef_compensation_arret = 7 ; // coefficient pour compenser l'arrêt. Après arret de l'alimenattion des des moteurs, du fait de l'inertie le robot continue d'avancer quelques secondes.
int nb_passage = 0 ;
int compt_nb_passage = 1 ;

//################################################################################################################################################################################
// Initialisation des dimension du terrain de badminton
int largeur_terrain = 120 ; //cm
int longueur_terrain = 100 ; //cm
//################################################################################################################################################################################


// ********************************************************************************************************************************************************************************
// Setpup - initialisation des fonctions
// ********************************************************************************************************************************************************************************

void setup() {
  // initialize serial communication at 9600 bits per second:
      Serial.begin(9600);
      Serial.println("DébutSetup");
  // Intialisation des interruptions pour le calcul des compteurs des encodeurs de chaque moteur pour alimenter la fonction d'asservissement des moteurs -----------------------------
  attachInterrupt(digitalPinToInterrupt(interruptPin_MotAvGa), F_cpt_MotAvGa, CHANGE);
  attachInterrupt(digitalPinToInterrupt(interruptPin_MotAvDr), F_cpt_MotAvDr, CHANGE);
  attachInterrupt(digitalPinToInterrupt(interruptPin_MotArGa), F_cpt_MotArGa, CHANGE);
  attachInterrupt(digitalPinToInterrupt(interruptPin_MotArDr), F_cpt_MotArDr, CHANGE);  
  // Intialisation de l'interruption pour le calcul du compteur de l'encodeur du moteur pour alimenter la fonction de calcul de la distance parcoure par le robot -------------------
  attachInterrupt(digitalPinToInterrupt(interruptPin_Dist), F_cpt_Dist, CHANGE);

  // Initialisation du timer pour le calcul périodique de l'asservissement des 4 moteurs d'netrainement du robot --------------------------------------------------------------------
  int FreqTimer=1000/frequence_echantillonnage;
  timer_MoteursDeplacement.setInterval(FreqTimer,asservissement_MoteursDeplacement); // Interruption pour calcul du PID et asservissement; toutes les 10ms, on recommence la routine

  // Initialisation de l'algorithme de balayage -------------------------------------------------------------------------------------------------------------------------------------
  //Calcul du nombre de passage
  nb_passage = largeur_terrain / largeur_robot;
  ref_Temps = millis(); // Initialisation  du compteur temps pour calculer un temps d'attente avant le mouvement suivant
      Serial.print("Consigne du nbre de passage");
      Serial.println(nb_passage);
    
      Serial.println("FinSetup");
}

// ********************************************************************************************************************************************************************************
// Loop - Boucle principale
// ********************************************************************************************************************************************************************************

void loop() {
 // Lancement du timer d'asservissement des moteurs avec encodeurs ---------------------------------------------------------------------------------------------------------------
 timer_MoteursDeplacement.run();  //on fait tourner l'horloge

 // Algorithme de traitement du séquentiel de déplacement du robot  ---------------------------------------------------------------------------------------------------------------
 // Définit la consigne de vitesse, la distance à pourcourir, le type de mouvement à réaliser  ------------------------------------------------------------------------------------
 // Le balayage du terrain est effectué en X traversées (appelées passage) chaque passage est composer de 3 mouvements : Marche avant pour balayer la longueur du terrain,*
 // déplacement latéral de la largeur du robot - x cm (pour garantir un balayage complet et pour finir une rotation de 180°.
 
  if (compt_nb_passage < nb_passage+1)
  { 
     if (Phase == 0)  //  Phase 0 : Traversée du terrain
      {
        mes_Temps = millis ();
        duration = mes_Temps-ref_Temps ;
        if( (duration) > 500)
        {
              Serial.println("J'avance");
          consigne_Dist = longueur_terrain;
          consigne_des_moteurs = 5;
          goForward();
        }
      }
    
      if (Phase== 1)  // Phase 1 : déplacement latéral droit ou gauche en du modulo du n° de traversé du terrain
      {
        mes_Temps = millis ();
        duration = mes_Temps-ref_Temps ;
        if( (duration) > 500)
        {
            if (compt_nb_passage%2 ==1)
          {
               Serial.println("Je me déplace à droite");
            consigne_Dist = largeur_robot;
            consigne_des_moteurs = 6;
            moveRight();
            Arret_Moteurs = false ;    }
           else if (compt_nb_passage%2 ==0)
           {
                Serial.println("Je me déplace à gauche");
            consigne_Dist = 50;
            consigne_des_moteurs = 6;
            moveLeft();
            Arret_Moteurs = false ; 
           }
        }
      }
    
      if (Phase== 2)  // Phase 2 : retournement complet du robot(180°) 
      {
        mes_Temps = millis ();
        duration = mes_Temps-ref_Temps ;
        if( (duration) > 500)
        {
              Serial.println("Je fais demi-tour");
          consigne_Dist = longueur_demi_tour;
          consigne_des_moteurs = 4.5;
          turnRight();
          Arret_Moteurs = false ; 
        }
      }
      if (Phase== 3) // Phase 3 : phase de cloture et d'incrément du compteur de nbre de passage
        {
              Serial.print("Nbre de passage = ");
              Serial.println(compt_nb_passage);
          compt_nb_passage++;
          Phase = 0;
        }
  }

 // Calcul de la distance parcourue par le robot pour arrêter déplacement du robot------------------------------------------------------------------------------------------------------
  Fct_CalculDistance ();

// Fin Boucle de traitement du séquentiel de gestion du balayage de la surface du terrain-----------------------------------------------------------------------------------------------
}

// ********************************************************************************************************************************************************************************
// Déclaration de toutes les fonctions
// ********************************************************************************************************************************************************************************


// Fonction asservissement des moteurs de déplacement  *********************************************************************************************************************************
void asservissement_MoteursDeplacement()
{
  if (Arret_Moteurs == false)  // Si la distance parcourue est supérieure à la consigne, le flag Arret_Moteurs est à vrai 
    //et le calcul d'asservissement ne doit pas s'executer pour ne pas envoyer de nouvelle consignes aux moteurs
    {
       // Calcul asservissement Moteur AvGa ------------------------------------------------------------------------
      // Calcul du nombre de tick de la codeuse du moteur par seconde : Frequence Echan * tick_codeuse
      int frequence_codeuse_MotAvGa = frequence_echantillonnage*compt_MotAvGa; 
      // Calcul de la vitesse de la roue
      float vit_roue_tour_sec_MotAvGa = (float)frequence_codeuse_MotAvGa/k_reductionMoteurs ;  
      // calcul erreur pour chaque composante du PID
      float erreur_MotAvGa = consigne_des_moteurs - vit_roue_tour_sec_MotAvGa; // pour le proportionnel
      somme_erreur_MotAvGa += erreur_MotAvGa; // pour l'intégrateur
      float delta_erreur_MotAvGa = somme_erreur_MotAvGa-erreur_precedente_MotAvGa;  // pour le dérivateur
      erreur_precedente_MotAvGa = erreur_MotAvGa;
      // PID : calcul de la commande pour chaque moteur -----------------------------------
      vit_MotAvGa = kp_MotAvGa*erreur_MotAvGa + ki_MotAvGa*somme_erreur_MotAvGa + kd_MotAvGa*delta_erreur_MotAvGa;  //somme des tois erreurs
       // Réinitialisation du nombre de tick de la codeuse ----------------------------------
      compt_MotAvGa = 0;
      // Normalisation et contrôle des moteurs --------------------------------------------
      if (vit_MotAvGa > 255) {
          vit_MotAvGa = 255;  // sachant que l'on est branché sur un pont en H L293D
        }   else if (vit_MotAvGa <0) {
          vit_MotAvGa = 0;
        }
      
      // Calcul asservissement Moteur AvDr ------------------------------------------------------------------------
      // Calcul du nombre de tick de la codeuse du moteur par seconde : Frequence Echan * tick_codeuse
      int frequence_codeuse_MotAvDr = frequence_echantillonnage*compt_MotAvDr; 
      // Calcul de la vitesse de la roue
      float vit_roue_tour_sec_MotAvDr = (float)frequence_codeuse_MotAvDr/k_reductionMoteurs;  
      // calcul erreur pour chaque composante du PID
      float erreur_MotAvDr = consigne_des_moteurs - vit_roue_tour_sec_MotAvDr; // pour le proportionnel
      somme_erreur_MotAvDr += erreur_MotAvDr; // pour l'intégrateur
      float delta_erreur_MotAvDr = somme_erreur_MotAvGa-erreur_precedente_MotAvDr;  // pour le dérivateur
      erreur_precedente_MotAvDr = erreur_MotAvDr;
      // PID : calcul de la commande pour chaque moteur -----------------------------------
      vit_MotAvDr = kp_MotAvDr*erreur_MotAvDr + ki_MotAvDr*somme_erreur_MotAvDr + kd_MotAvDr*delta_erreur_MotAvDr;  //somme des tois erreurs
       // Réinitialisation du nombre de tick de la codeuse ----------------------------------
      compt_MotAvDr = 0;
      // Normalisation et contrôle des moteurs --------------------------------------------
      if (vit_MotAvDr > 255) {
          vit_MotAvDr = 255;  // sachant que l'on est branché sur un pont en H L293D
        }   else if (vit_MotAvDr <0) {
          vit_MotAvDr = 0;
        }
    
      // Calcul asservissement Moteur ArGa ------------------------------------------------------------------------
      // Calcul du nombre de tick de la codeuse du moteur par seconde : Frequence Echan * tick_codeuse
      int frequence_codeuse_MotArGa = frequence_echantillonnage*compt_MotArGa; 
      // Calcul de la vitesse de la roue
      float vit_roue_tour_sec_MotArGa = (float)frequence_codeuse_MotArGa/k_reductionMoteurs;  
      // calcul erreur pour chaque composante du PID
      float erreur_MotArGa = consigne_des_moteurs - vit_roue_tour_sec_MotArGa; // pour le proportionnel
      somme_erreur_MotArGa += erreur_MotArGa; // pour l'intégrateur
      float delta_erreur_MotArGa = somme_erreur_MotArGa-erreur_precedente_MotArGa;  // pour le dérivateur
      erreur_precedente_MotArGa = erreur_MotArGa;
      // PID : calcul de la commande pour chaque moteur -----------------------------------
      vit_MotArGa = kp_MotArGa*erreur_MotArGa + ki_MotArGa*somme_erreur_MotArGa + kd_MotArGa*delta_erreur_MotArGa;  //somme des tois erreurs
       // Réinitialisation du nombre de tick de la codeuse ----------------------------------
      compt_MotArGa = 0;
      // Normalisation et contrôle des moteurs --------------------------------------------
      if (vit_MotArGa > 255) {
          vit_MotArGa = 255;  // sachant que l'on est branché sur un pont en H L293D
        } 
        else if (vit_MotArGa <0) {
          vit_MotArGa = 0;
        } 
      
      // Calcul asservissement Moteur ArDr ------------------------------------------------------------------------
      // Calcul du nombre de tick de la codeuse du moteur par seconde : Frequence Echan * tick_codeuse
      int frequence_codeuse_MotArDr = frequence_echantillonnage*compt_MotArDr; 
      // Calcul de la vitesse de la roue
      float vit_roue_tour_sec_MotArDr = (float)frequence_codeuse_MotArDr/k_reductionMoteurs ;  
      // calcul erreur pour chaque composante du PID
      float erreur_MotArDr = consigne_des_moteurs - vit_roue_tour_sec_MotArDr;      // pour le proportionnel
      somme_erreur_MotArDr += erreur_MotArDr;                                       // pour l'intégrateur
      float delta_erreur_MotArDr = somme_erreur_MotArGa-erreur_precedente_MotArDr;  // pour le dérivateur
      erreur_precedente_MotArDr = erreur_MotArDr;
      // PID : calcul de la commande pour chaque moteur -----------------------------------
      vit_MotArDr = kp_MotArDr*erreur_MotArDr + ki_MotArDr*somme_erreur_MotArDr + kd_MotArDr*delta_erreur_MotArDr;  //somme des tois erreurs
       // Réinitialisation du nombre de tick de la codeuse ----------------------------------
      compt_MotArDr = 0;
      // Normalisation et contrôle des vitesses moteurs --------------------------------------------
      if (vit_MotArDr > 255) {
          vit_MotArDr = 255;  // sachant que l'on est branché sur un pont en H L293D
        }   else if (vit_MotArDr <0) {
          vit_MotArDr = 0;
        } 
      // Envoie de la nouvelle référence vitesse à chaque moteur ----------------
      motorArDr.setSpeed(vit_MotArDr);
      motorArGa.setSpeed(vit_MotArGa);
      motorAvDr.setSpeed(vit_MotAvDr);
      motorAvGa.setSpeed(vit_MotAvGa);
  }
}

// Fonction de calcul de la distance parcourue par le robot. Cette fonction est déclenchée par une interruption connectée au codeur numéro 2 d'une des roue du robot ******************
void Fct_CalculDistance ()
{
 //Calcul de la distance
Dist = compt_Dist * k_reductionDistance ;
  if (Dist >= (consigne_Dist-coef_compensation_arret)) // Arrêt du robot si la distance parcourue est >= à la consigne
  {
          Serial.print("Distance calculée = ");
          Serial.print(Dist);
          Serial.print("  Nombre d'impulsion du compteur = ");
          Serial.println (compt_Dist);
    hardStop(); // déclenchement de l'arrêt des moteurs
    Arret_Moteurs = true; // Flag d'arrêt des moteurs à "VRAI" ... permet de courcuiter le traitement de la fonction asservissement
    compt_Dist=0; // remise à zéro du compteur de distance
    ref_Temps = millis(); // Initialisation  du compteur temps pour calculer un temps d'attente avant le mouvement suivant
    Phase++; // Incrément du compteur de phase pour l'algorithme séquenciel de balayage
  } 
}

// Fonctions comptage des tick des encodeurs des moteurs. Ces fonctions sont déclenchées sur interruption ******************************************************************************
void F_cpt_MotAvGa() {  compt_MotAvGa++; }
void F_cpt_MotAvDr() {  compt_MotAvDr++; }
void F_cpt_MotArGa() {  compt_MotArGa++; }
void F_cpt_MotArDr() {  compt_MotArDr++; }
void F_cpt_Dist()    {  compt_Dist++;    }

// Fonctions definissant les mouvements élémentaires du robot ***********************************************************************************************************************

void goForward(){
  motorAvDr.run(FORWARD);
  motorAvGa.run(FORWARD);
  motorArDr.run(FORWARD);
  motorArGa.run(FORWARD);
}// void goForward()

void goBackward(){
  motorAvDr.run(BACKWARD);
  motorAvGa.run(BACKWARD);
  motorArDr.run(BACKWARD);
  motorArGa.run(BACKWARD);  
}// void goBackwad()

void moveRight(){
  motorAvDr.run(BACKWARD);
  motorAvGa.run(FORWARD);
  motorArDr.run(FORWARD);
  motorArGa.run(BACKWARD);
}// void moveRight()

void moveLeft(){
  motorAvDr.run(FORWARD);
  motorAvGa.run(BACKWARD);
  motorArDr.run(BACKWARD);
  motorArGa.run(FORWARD);
}// void moveLeft()

void turnRight(){
  motorAvDr.run(BACKWARD);
  motorAvGa.run(FORWARD);
  motorArDr.run(BACKWARD);
  motorArGa.run(FORWARD);
}// void turnRight()

void turnLeft(){
  motorAvDr.run(FORWARD);
  motorAvGa.run(BACKWARD);
  motorArDr.run(FORWARD);
  motorArGa.run(BACKWARD);
}// void turnRight()

void hardStop(){
  motorAvDr.run(RELEASE);
  motorAvGa.run(RELEASE);
  motorArDr.run(RELEASE);
  motorArGa.run(RELEASE);
}// void hardRobot()

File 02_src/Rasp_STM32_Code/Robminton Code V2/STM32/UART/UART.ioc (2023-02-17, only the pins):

Mcu.UserName=STM32L476RGTx
PA2.GPIO_Label=USART_TX
PA2.Signal=USART2_TX
PA3.GPIO_Label=USART_RX
PA3.Signal=USART2_RX
PA5.GPIO_Label=LD2 [green Led]
PA5.Signal=GPIO_Output
PC0.GPIO_Label=IN4_Motor
PC0.Signal=GPIO_Output
PC1.GPIO_Label=IN3_Motor
PC1.Signal=GPIO_Output
PC13.GPIO_Label=B1 [Blue PushButton]
PC13.Signal=GPXTI13

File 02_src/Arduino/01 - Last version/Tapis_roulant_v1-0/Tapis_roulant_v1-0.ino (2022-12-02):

int M1_1A = 4;
int M1_1B = 5;
int M1_P_1 = 9;
int M2_2A = 7;
int M2_2B = 8;
int M2_P_2 = 10;
int M1et2_Enable = 6;
int i=0;
//interruption
int interruptCaptIRGa=2;
int interruptCaptIRDr=3;
int interruptMotTapisGa=18;
int interruptMotTapisDr=19;
int Cpt_CaptIRGa=0;
int Cpt_CaptIRDr=0;
int Cpt_EncodeurMotTapisGa=0;
int Cpt_EncodeurMotTapisDr=0;
int erreur_Synchro=0;
float correction_dif=0;
float kDif =0.01;
boolean CoteSyncGa = false;
boolean CoteSyncDr = false;
unsigned long time_MillisGa=0;
unsigned long time_MillisDr=0;
int erreur_synchro_Millis =0;
int k_time_MillisGa = 0 ;
int k_time_MillisDr = 0 ;
int Offset_comptGa = 0;

// Déclaration timer ***********************************************************************************
#include <SimpleTimer.h>
SimpleTimer timerElevateur;
const int frequence_echantillonnage = 20;  // Fréquence d'exécution de l'asservissement (Xxx fois par seconde)
int periode_echantillonage=1000/frequence_echantillonnage;
// Déclaration des caractéristique du moteur ***********************************************************
const int rapport_reducteur_Mots = 40;   // Rapport entre le nombre de tours de l'arbre moteur et de la roue
const int tick_par_tour_codeuse_Mots = 12;  //12 tick sur deux capteurs hall, ici on a pris un seul capteur mais 2 front
// Déclaration des constantes et variables du PID *******************************************************
// Déclaration des constantes ********************************
// Moteur 1 = moteur Droit = Port M1 sur le pont en H.
float kp_Mot1 = 50;     // coefficient proportionnel
float ki_Mot1 = 20;       // Coefficient intégrateur
float kd_Mot1 = 10;     // Coefficient dérivateur
float kp_Mot2 = 50;     // coefficient proportionnel
float ki_Mot2 = 20;       // Coefficient intégrateur
float kd_Mot2 = 10;     // Coefficient dérivateur

// Initialisation des variables *******************************
int vitMot_1 = 0;
float consigne_Mot1 = 2.4; // consigne en nombre de tours de roue par seconde
float erreur_precedente_Mot1 = consigne_Mot1;
float somme_erreur_Mot1 = 0;
int vitMot_2 = 0;
float consigne_Mot2 = 2.4;
float erreur_precedente_Mot2 = consigne_Mot2;
float somme_erreur_Mot2 = 0;


void setup() { 
  
  // Motor_1 controll pin initiate; 
  pinMode(M1_1A, OUTPUT); 
  pinMode(M1_1B, OUTPUT); 
  pinMode(M1_P_1, OUTPUT);   // Speed control 
  // Motor_2 controll pin initiate; 
  pinMode(M2_2A, OUTPUT); 
  pinMode(M2_2B, OUTPUT); 
  pinMode(M2_P_2, OUTPUT); // Speed control 
  //Enable the Motor Shield output; 
  pinMode(M1et2_Enable, OUTPUT); 
  digitalWrite(M1et2_Enable, HIGH);
   
  // Initialisation liaison série
  Serial.begin(19200);
  Serial.println("Begin");

  //synchronisation tapis
  
  syncTapis();
  delay(3000);

  // initialialisation interruption pour compensation des écarts de courroies
  attachInterrupt(digitalPinToInterrupt(interruptCaptIRGa), fct_SynchroIRGa, FALLING);
  attachInterrupt(digitalPinToInterrupt(interruptCaptIRDr), fct_SynchroIRDr, FALLING);
  time_MillisGa = millis();
  time_MillisDr = millis();

  attachInterrupt(digitalPinToInterrupt(interruptMotTapisGa), fct_EncodeurMotTapisGa, CHANGE);
  attachInterrupt(digitalPinToInterrupt(interruptMotTapisDr), fct_EncodeurMotTapisDr, CHANGE);
    // Initialisation du timer-----------------------------------------------------------------------------
 
  Serial.print("periode_echantillonage = ");
  Serial.println(periode_echantillonage);
  timerElevateur.setInterval(periode_echantillonage,asservissement_Mots); // Interruption pour calcul du PID et asservissement; toutes les 10ms, on recommence la routine

  } 
 
  void loop() { 
  
  // Boucle pour asservissement des moteurs avec encodeurs -----------------------------------------------
  timerElevateur.run();  //on fait tourner l'horloge
  delay(10);
// Fin Boucle pour asservissement des moteurs avec encodeurs ---------------------------------------------
  }


void syncTapis()
{

  //interruption 
  attachInterrupt(digitalPinToInterrupt(interruptCaptIRGa), fct_CaptIRGa, FALLING);
  attachInterrupt(digitalPinToInterrupt(interruptCaptIRDr), fct_CaptIRDr, FALLING);

  //lancement rotation à vitess maxi pour synchronisation
  analogWrite(M2_P_2,255); // set the motor_2 speed ; 
  analogWrite(M1_P_1,255); // set the motor_1 speed ;
  digitalWrite(M2_2A, HIGH); 
  digitalWrite(M1_1A, LOW); 
  digitalWrite(M2_2B, LOW); // Set the rotation of motor_2 
  digitalWrite(M1_1B, HIGH); // Set the rotation of motor_1 

  
   //interruption
   Serial.println("Lancement synchronisation");
    do 
    {
     /*
      Serial.print("Cpt_CaptIRGa=");
      Serial.print(Cpt_CaptIRGa);
      Serial.print("  Cpt_CaptIRDr=");
      Serial.println(Cpt_CaptIRDr);
    */  
          if (Cpt_CaptIRGa >= 1)
        {
          analogWrite(M2_P_2,0); // set the motor_2 stop ; 
         // Serial.println("Mousse sous capteur Gauche");
          Cpt_CaptIRGa=0;
          CoteSyncGa = true;
        }
        if (Cpt_CaptIRDr >= 1)
        {
          analogWrite(M1_P_1,0); // set the motor_1 stop ; 
         // Serial.println("Mousse sous capteur Droit");
          Cpt_CaptIRDr=0;
          CoteSyncDr = true;
        }
        delay (100);
    }while(CoteSyncGa == false || CoteSyncDr == false);
    Serial.println("Fin de synchro");
    
    //detacher interruption 
    detachInterrupt(digitalPinToInterrupt(interruptCaptIRGa));
    detachInterrupt(digitalPinToInterrupt(interruptCaptIRDr));
}

void moveTapis ()
{
  //lancement rotation à vitess maxi pour synchronisation
  analogWrite(M2_P_2,255); // set the motor_2 speed ; 
  analogWrite(M1_P_1,255); // set the motor_1 speed ;
  digitalWrite(M2_2A, HIGH); 
  digitalWrite(M1_1A, LOW); 
  digitalWrite(M2_2B, LOW); // Set the rotation of motor_2 
  digitalWrite(M1_1B, HIGH); // Set the rotation of motor_1 

}

void fct_CaptIRGa()
{
  Cpt_CaptIRGa++;
}
void fct_CaptIRDr()
{
  Cpt_CaptIRDr++;
}
void fct_EncodeurMotTapisGa()
{
  Cpt_EncodeurMotTapisGa++;
}
void fct_EncodeurMotTapisDr()
{
  Cpt_EncodeurMotTapisDr++;
}
void fct_SynchroIRGa()
{
  time_MillisGa=millis();
  k_time_MillisGa=1; 
}
void fct_SynchroIRDr()
{
  time_MillisDr=millis();
  k_time_MillisDr=1;
}
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

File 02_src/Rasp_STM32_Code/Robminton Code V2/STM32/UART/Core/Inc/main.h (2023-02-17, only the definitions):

#define B1_Pin GPIO_PIN_13
#define B1_GPIO_Port GPIOC
#define IN4_Motor_Pin GPIO_PIN_0
#define IN4_Motor_GPIO_Port GPIOC
#define IN3_Motor_Pin GPIO_PIN_1
#define IN3_Motor_GPIO_Port GPIOC
#define USART_TX_Pin GPIO_PIN_2
#define USART_TX_GPIO_Port GPIOA
#define USART_RX_Pin GPIO_PIN_3
#define USART_RX_GPIO_Port GPIOA
#define LD2_Pin GPIO_PIN_5
#define LD2_GPIO_Port GPIOA
#define TMS_Pin GPIO_PIN_13
#define TMS_GPIO_Port GPIOA
#define TCK_Pin GPIO_PIN_14
#define TCK_GPIO_Port GPIOA
#define SWO_Pin GPIO_PIN_3
#define SWO_GPIO_Port GPIOB

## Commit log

2022-11-25 Init Repo
    [nut_rs20.SLDPRT, profil_alu_rs20_efrei.SLDPRT, support_moteur_rs4.SLDPRT]
2022-12-02 add previous version
    [Pièce Entonoir droite.SLDPRT, Pièce Entonoir gauche.SLDPRT]
2022-12-16 ajout equerre
    [equerre.SLDPRT]
2023-01-06 ajout entonnoir
    [Assemblage.SLDASM, cote.SLDPRT, haut_bas.SLDPRT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]
2023-01-10 Fichier solidWorks pour le chassis, le support moteur et le chasse-volant
    [Chasse-volant V1.SLDPRT, Chassis.SLDASM, support_moteur_complet.SLDPRT]
2023-01-10 Ajout fichiers SolidWorks
    [Chassis.SLDASM, Robot.SLDASM, support_moteur_rs4.SLDPRT]
2023-01-12 Ajout/Modification de fichiers SolidWorks
    [Modélisation_moteur.SLDPRT, Modélisation_roue.SLDPRT, Robot.SLDASM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]
2023-01-12 Ajout fichier solidWorks
    [profil_alu_rs20_efrei - longueur.SLDPRT]
2023-01-19 V2 entonnoir new robot
    [Assemblage.SLDASM, Robot.SLDASM, cote.SLDPRT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]
2023-01-20 Ajout fichiers SolidWorks (robot complet et lanceur)
    [1er cylindre test.SLDPRT, 2e cylindre épouse forme.SLDPRT, 3e cylindre 8 trous.SLDPRT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]
2023-01-20 Ajout Support Moteur
    [supportNucleo_rs20.SLDPRT, support_moteur_rs4.SLDPRT]
2023-02-02 Add files via upload
    update du lanceur
    [1er cylindre test.SLDPRT, 2e cylindre épouse forme.SLDPRT, 3e cylindre 8 trous.SLDPRT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]
2023-02-02 Ajout du nouveau support de moteur
    [support moteur V2.SLDPRT]
2023-02-03 Ajout du code communication raspi et STM32
2023-02-10 Support moteur
    [support moteur V2.SLDPRT]
2023-02-10 correction fichiers entonnoir
    [fixation_plate_entonnoir_V2.SLDPRT, rouleau_V3.SLDPRT]
2023-02-10 robot avec nouveau support moteur
    [Robot.SLDASM]
2023-02-17 correction assemblage et nouvelle equerre
    [equerre_2_V1.SLDPRT, equerre_V2.SLDPRT, fixation_plate_entonnoir_V3.SLDPRT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]
2023-02-17 ajout support moteur definitif + code Amon
    [Robot.SLDASM, support moteur V2.SLDPRT, support moteur V3.SLDPRT]
2023-02-26 ajout couvercle pour le support moteur
    [couvercle support moteur.SLDPRT, support moteur V3.SLDPRT, support moteur V3.STL]
2023-02-26 Update main.cpp
    Ajout de la hauteur max
2023-02-27 maj lanceur
    [support_moteur_drone_VF.SLDPRT, support_moteur_drone_VF_mesure.SLDPRT]
2023-02-27 Update main.cpp
    Correction de quelques erreurs
    [main.cpp]
2023-03-10 ajout pièces SW
    [Robot.SLDASM, couvercle support moteur.SLDPRT, couvercle support moteur.STL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]
2023-03-17 ajout piece entonnoir
    [accroche_cote.SLDPRT, accroche_cote_2.SLDPRT, equerre_2_V1.STL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]
2023-03-23 Modif SW
    [Chassis.SLDASM, Robot.SLDASM, Support Hardware.SLDPRT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]
2023-03-23 modif support HW
    [Support Hardware.SLDPRT, robot_entonnoir_V4.SLDASM, supportNucleo_rs20.SLDPRT]
2023-03-24 modif git
    [Bottom_Hex_SM.stl, Top_H20_Slots_SM.stl]
2023-03-29 tri pieces lanceur
    [1er cylindre test.SLDPRT, 2e cylindre épouse forme.SLDPRT, 3e cylindre 8 trous.SLDPRT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]
2023-03-29 ajout plaques entonnoir
    [accroche_cote_droite.SLDPRT, accroche_cote_gauche.SLDPRT, plaque.SLDPRT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]

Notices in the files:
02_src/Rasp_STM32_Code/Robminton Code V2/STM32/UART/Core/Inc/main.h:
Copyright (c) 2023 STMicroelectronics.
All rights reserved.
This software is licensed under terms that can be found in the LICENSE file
